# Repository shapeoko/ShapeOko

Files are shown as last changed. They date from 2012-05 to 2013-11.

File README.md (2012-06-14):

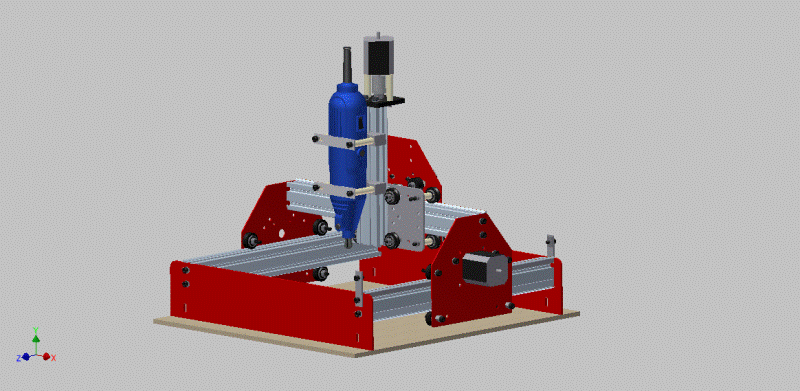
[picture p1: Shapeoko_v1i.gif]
Shapeoko v1i


Goal: ShapeOko's goal is to design and build a fully open source (open hardware) 3 axis CNC machine that anyone can build for about $300. We're doing everything possible to design an easy to assembly, fully capable machine that will do it's part in both the open hardware and desktop manufacturing movements.

#Folder Structure#

##Build_Instructions##
Contains the source files for the PDf build instruction manual (quick start guide). The original document was created in Scribus 1.4.1 an open source Desktop Publishing app that is cross platform compatible. The placed images (PDF files) are all embedded in the document, but can be replaced with the PDF files found in the drawings_pdf folder under the root of the repository. Improvements are encouraged, please contact me for a merge request.

###individual_pages##
Individual pages of the PDF build instruction manual. These are used as targets from the wiki.

##Documents##
Contains informational documentation related to the project. This would include data sheets for purchased electrical components, Bill of Material Information, and an assortment of other miscelaneous documents. Please feel free to suggest more documents that are not currently included.

##drawings_pdf##
PDF exports of the original 2D drawing files. PDF is as universal format as any, publishing in this format will allow anyone to open and view the drawing files without having to install a specialty CAD program. PDF was chosen over DXF for the time being. Community generated DXF files from the original drawings files (drawings_idw) are welcome.

##exploded_png##
There is a non-annotated image at the top of each assiciated page of the wiki. Those images can be found in this directory.

##reference_images##
Image files associated with the project. Logos, and standard views.

##upgrades##
Complete zip files of upgrades for your machine. Currently this is limited to two (2) variations of the standard spindle mount. 

##README.md##
This document in markdown format.

##Shapeoko_v1i##
Image file referenced at the top of this document. 

##Shapeoko_v1i.zip##
Complete Autodesk Inventor Project file for the Shapeoko CNC machine. All part (.ipt), presentation (.ipn), drawing (.idw), and assembly (.iam) files are included in this file. This is probably the place to start if you're looking to import the 3D model. 

###For more information:###
- website: www.shapeoko.com
- wiki: www.shapeoko.com/wiki
- forum: www.shapeoko.com/forum
- twitter: @shapeoko

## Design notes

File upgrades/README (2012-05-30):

Set of drawings, 3D models, images, and gcode files. These sets can be used as a reference to "upgrade" your ShapeOko Machine. Each set is packaged into a seperate zip file. For more information on each set see the "Upgrades" section at www.shapeoko.com

Dremel_mount - Set of UHMW mounts for a Standard Dremel (or generic) rotary tool. Something like this ($13USD) works great: http://www.truevalue.com/product/Fathers-Day/Handy-Dad/Rotary-Tools/40-Pc-Rotary-Tool-Kit/pc/2502/c/2525/sc/2557/36169.uts

DW660_Mount - Set of UHMW (or HDPE or Delrin or anything 3/8" or thicker) mounts for a Dewalt DW660 trim router. You can find this trim router on amazon's website for around $60USD. Link: http://www.amazon.com/DEWALT-DW660-Cut-Out-Rotary-Collets/dp/B000051WQX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

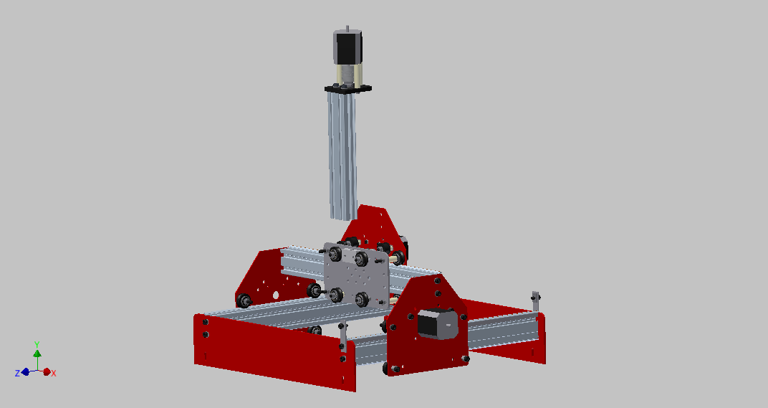
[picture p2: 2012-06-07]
exploded_png/SM-FA03.png

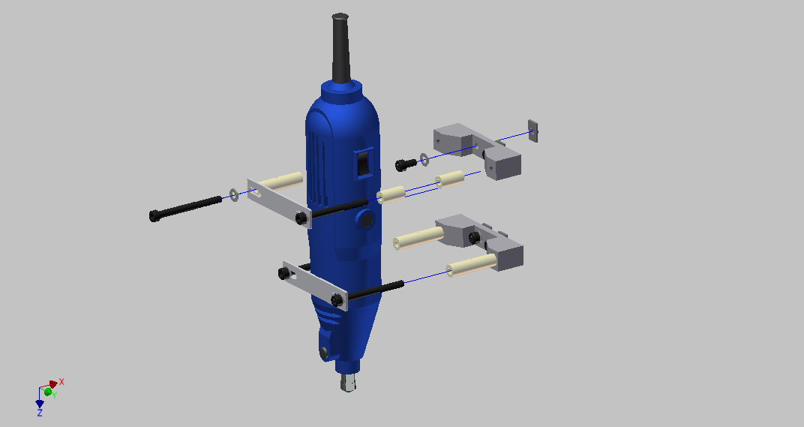
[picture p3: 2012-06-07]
exploded_png/SM-ZA03.png

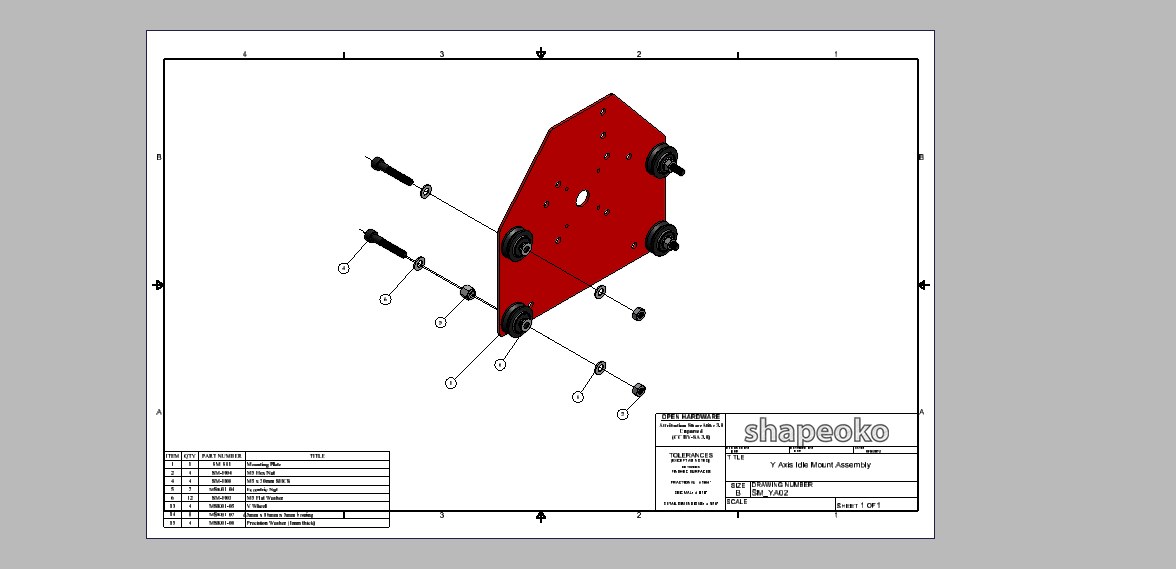
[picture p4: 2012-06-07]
drawings_png/SM-YA02.png

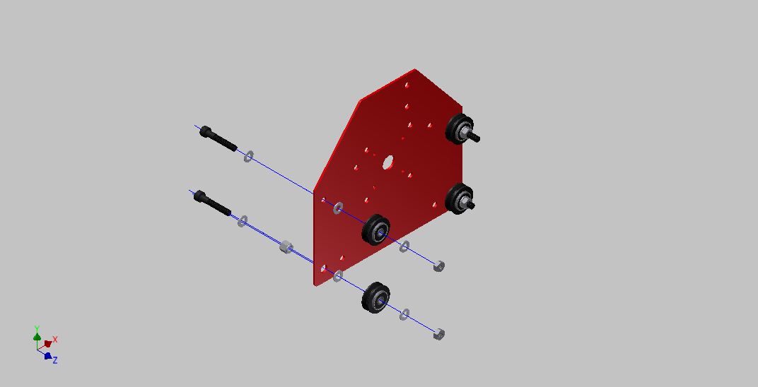
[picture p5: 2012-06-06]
exploded_png/SM-YA02.png

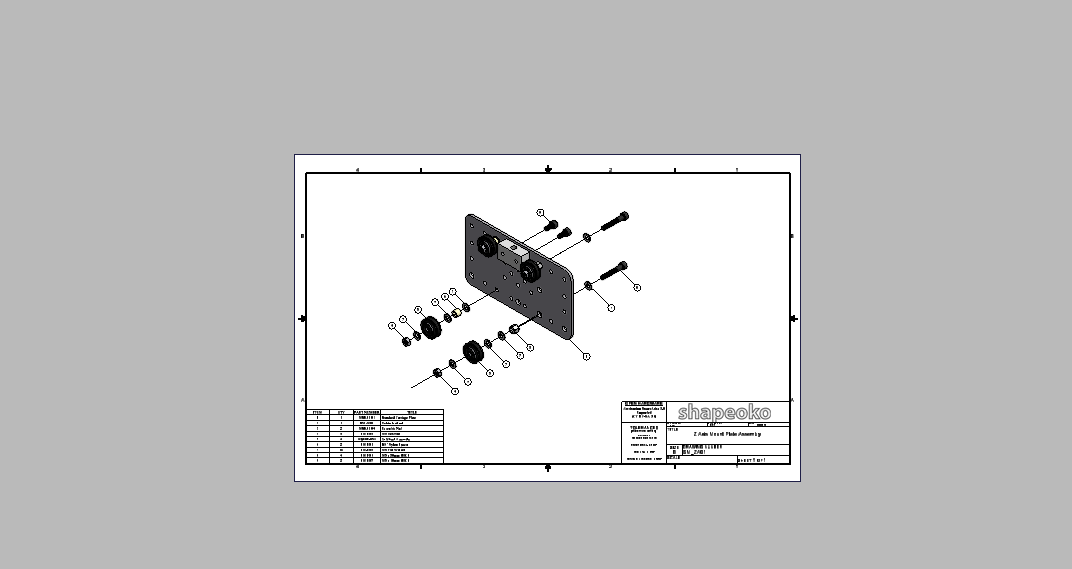
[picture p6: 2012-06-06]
drawings_png/SM-ZA01.png

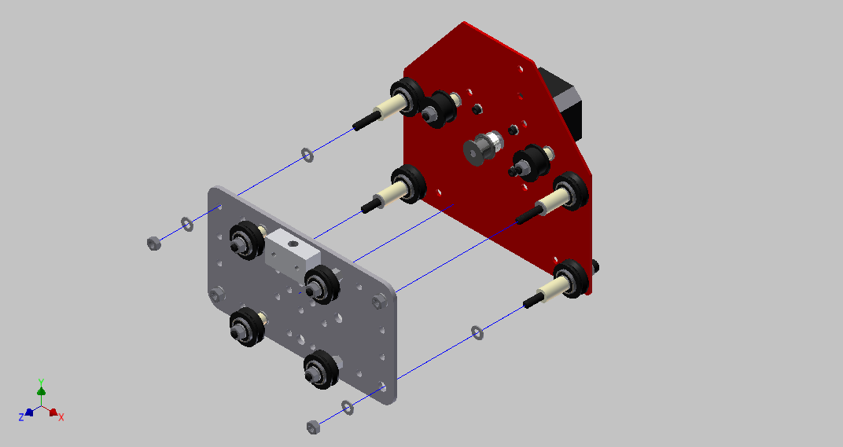
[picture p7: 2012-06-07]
exploded_png/SM-XZA1.png

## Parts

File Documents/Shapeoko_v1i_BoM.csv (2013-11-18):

Item | Project | Estimated Cost | Part Number | BOM Structure | Unit QTY | QTY | Vendor | Stock Number | Title | Web Link
1 | Shapeoko | $3.38 | MKS01-02 | Normal | 1 | 3 | buildlog.net | B17002-375 | Makerslide Extrusion - 375mm | http://store.makerslide.com/index.php?main_page=product_info&cPath=6&products_id=7
2 | Shapeoko | $5.00 | SM-S01 | Normal | 1 | 3 | Shapeoko | SM-S01 | Mounting Plate | www.shapeoko.com/purchase
3 | Shapeoko | $0.02 | SM-H04 | Purchased | 1 | 20 | McMasterCarr | 90592A012 | M5 Hex Nut
5 | Shapeoko | $0.09 | SM-H08 | Purchased | 1 | 16 | McMasterCarr | 91290A254 | M5 x 30mm SHCS
6 | Shapeoko | $2.00 | MSK01-04 | Normal | 1 | 8 | buildlog.net | B18001-001 | Eccentric Nut
7 | Shapeoko | $0.02 | SM-H03 | Purchased | 1 | 100 | McMasterCarr | SM-H03 | M5 Flat Washer
8 | Shapeoko | $5.90 | MSK01-09 | Purchased | 1 | 2 | SDP-SI | A 6T16M018DF6005 | 18 Tooth Timing Pulley | https://sdp-si.com/eStore/PartDetail.asp?Opener=Group&PartID=24069&GroupID=347
9 | Shapeoko | $15.00 | SM-E01 | Purchased | 1 | 3 | buildlog.net | B10-10001 | Nema17 Stepper Motor
10 | Shapeoko | $0.07 | SM-H01 | Purchased | 1 | 6 | McMasterCarr | RSN-10_04-M | 1/4 Nylon Spacer
12 | Shapeoko | $0.04 | SM-H14 | Purchased | 1 | 8 | McMasterCarr | 91290A113 | M3 x 8mm SHCS
13 | Shapeoko | $0.02 | SM-H15 | Purchased | 1 | 8 | McMasterCarr | 91166A210 | M3 Flat Washer
14 | Shapeoko | $0.06 | SM-H07 | Purchased | 1 | 20 | McMasterCarr | SM-H07 | M5 x 10mm SHCS
15 | Shapeoko | $8.00 | MSK01-01 | Normal | 1 | 1 | buildlog.net | C14005 | Standard Carriage Plate
16 | Shapeoko | $2.50 | SM-M08 | Normal | 1 | 1 | Shapeoko | SM-M08 | Delrin lead nut.
17 | Shapeoko | $0.22 | SM-H09 | Purchased | 1 | 8 | McMasterCarr | 91290A264 | M5 x 55mm SHCS
18 | Shapeoko | $0.09 | SM-H02 | Purchased | 1 | 18 | McMasterCarr | 94639A457 | 3/4 Nylon Spacer
19 | Shapeoko | $5.00 | SM-S02 | Normal | 1 | 2 | Shapeoko | SM-S02 | Front/Back Plate
20 | Shapeoko | $0.27 | SM-M05 | Purchased | 1 | 2 | McMasterCarr | 1394A31 | Belt Anchor
21 | Shapeoko | $0.16 | SM-H11 | Purchased | 1 | 6 | Misumi | HNKK5 | Insertion Nut
22 | Shapeoko | $5.00 | SM-S06 | Normal | 1 | 1 | ShapeOko | SM-S06 | Z-Axis Mount Plate
23 | Shapeoko | $0.16 | SM-H13 | Purchased | 1 | 2 | McMasterCarr | 91290A232 | M5 x 16mm SHCS
24 | Shapeoko | $1.00 | SM-M07 | Purchased | 1 | 1 | McMasterCarr | skate_bearing | Z-Axis Bearing
25 | Shapeoko | $0.05 | SM-H10 | Purchased | 1 | 2 | McMasterCarr | 90695A040 | M8 Jam Nut
26 | Shapeoko | $5.58 | SM-H12 | Purchased | 1 | 1 | Ebay | ebay | Coupler
27 | Shapeoko | $1.00 | SM-H05 | Purchased | 1 | 1 | McMasterCarr | 99055A125 | Threaded Rod
28 | Shapeoko | $2.00 | MSK01-03 | Normal | 1 | 1 | buildlog.net | B17022-200 | Makerslide Extrusion - 200mm
29 | Shapeoko | $0.20 | SM-H06 | Purchased | 1 | 3 | McMasterCarr | 91290A137 | M3 x 50mm SHCS
30 | Shapeoko | $5.00 | SM-TM1 | Normal | 1 | 2 | Shapeoko | SM-TM1 | Spindle Mount
31 | Shapeoko | $15.00 | SM-TM3 | Purchased | 1 | 1 | various | Multi-tool | Rotary Tool
32 | Shapeoko | $2.00 | SM-TM2 | Normal | 1 | 2 | Shapeoko | SM-TM2 | Spindle Strap
33 | Shapeoko |  | MDF_Base | Normal | 1 | 1 | various | SM-SWB | 400mm x 450mm MDF
34 |  |  | MSK01-05 | Purchased | 1 | 16 | buildlog.net |  | V Wheel
35 |  |  | MSK01-07 | Purchased | 1 | 40 | buildlog.net | BEARING_5_16_5 | 5mm x 16mm x 5mm bearing
36 |  |  | MSK01-08 | Normal | 1 | 20 | buildlog.net | B18026 | Precision Washer (1mm thick)
37 |  | $2.00 | MSK01-06 | Normal | 1 | 4 | buildlog.net | B17023 | Smooth Idler Drum

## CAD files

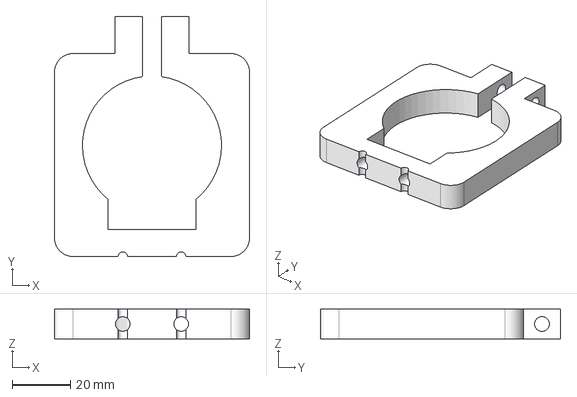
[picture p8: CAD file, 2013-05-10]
upgrades/dremel_mount/uhmw_dremel_mount_1-78.stp
66.8 x 82.2 x 10.2 mm

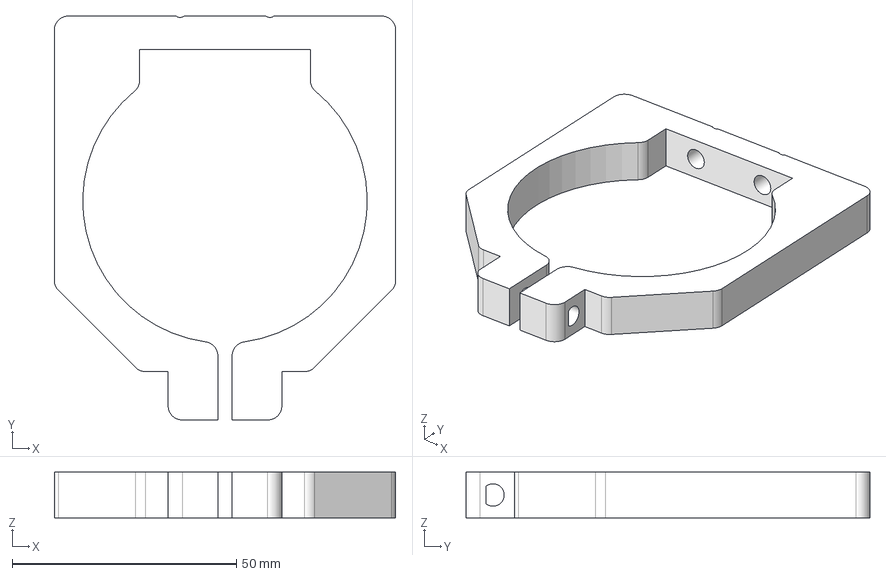
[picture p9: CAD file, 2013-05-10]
upgrades/dw660_mount/DW660_Mount.stp
76.2 x 90.2 x 10.2 mm

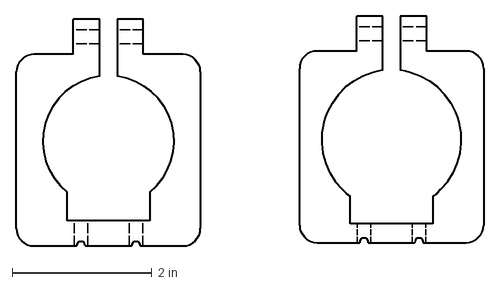
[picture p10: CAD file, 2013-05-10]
upgrades/dremel_mount/uhmw_dremel_mounts.dxf
6.68 x 3.29 in

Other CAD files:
upgrades/dremel_mount/uhmw_dremel_mount_2in.stp
upgrades/dremel_mount/uhmw_dremel_mount_1-78.stl
upgrades/dremel_mount/uhmw_dremel_mount_2in.stl
upgrades/dw660_mount/DW660_Mount.dxf

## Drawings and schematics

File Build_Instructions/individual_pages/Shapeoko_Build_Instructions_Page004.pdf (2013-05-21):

S

h

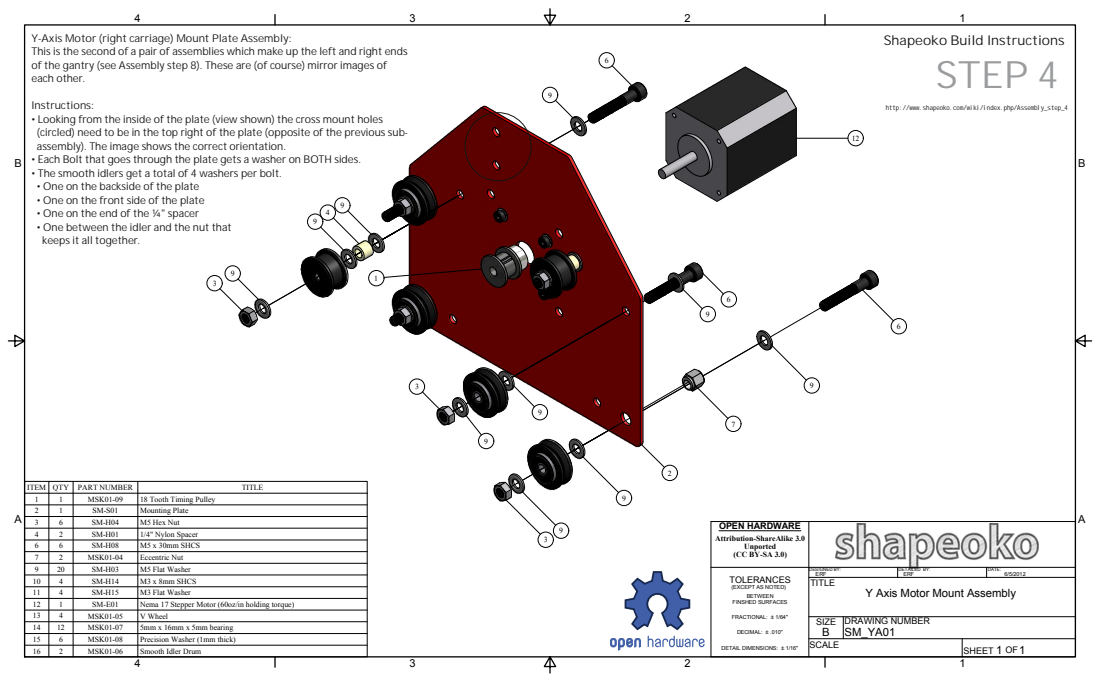
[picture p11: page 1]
uild In; ctio; /www.s; p/Ass; mbly_s; xis; rig; ria; Pla; sse; bly; ste; rse); mir; r. Instruction; s: • Looking fro m; sid; pla; (view; own; cro; ole; (circle; site; revio; bly). T; ows; rie; tio

bly: This is the second of a pair of assemblies which make u

peoko.com/wiki/index.ph

n. • Each Bolt that goes through the plate gets a washer
s. • The smooth idlers get a total of 4 washers per bolt. • One on the backside of the plate • One on the front side of the plate • One on the end of the ¼" spacer • One between the idler and the nut that keeps it all together.

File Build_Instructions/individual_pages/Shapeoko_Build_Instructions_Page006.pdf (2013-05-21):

S

h

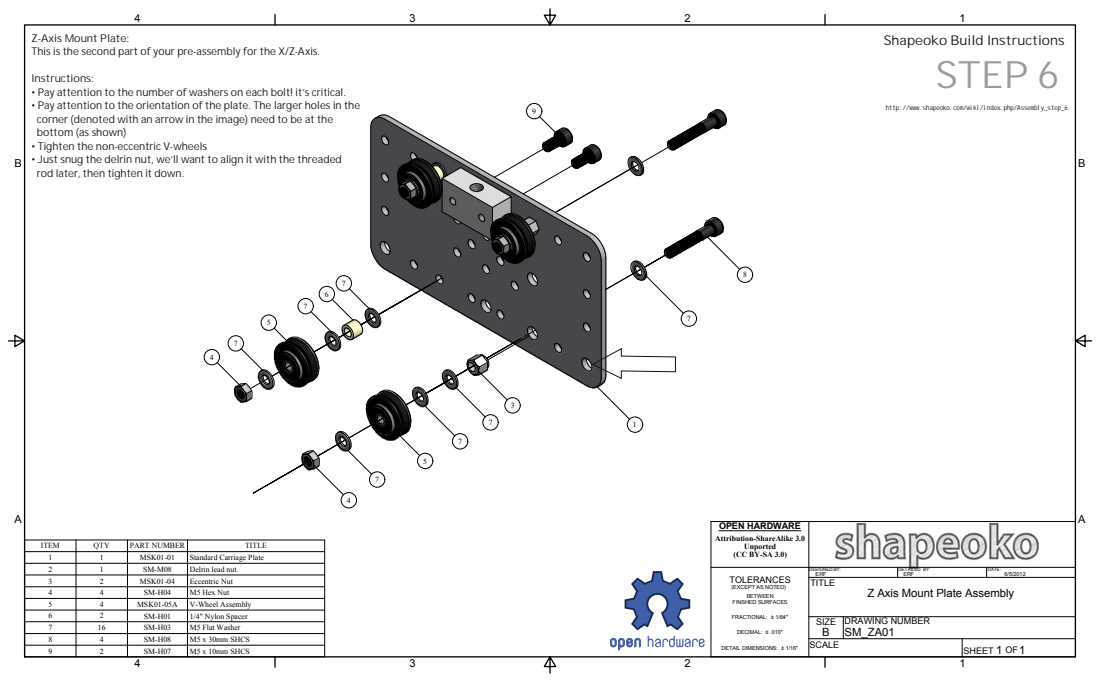
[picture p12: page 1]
uild In; tio; www.s; wiki/in; mbly; xis; Pla; bly; wit; Tig; ric; els; elrin; alig; tig

e: This is the second pa

xis. Instructions: • Pay attention to the number of washers on each bolt! it’s critic

al. • Pay attention to the orientation of the plate. The larger holes in t

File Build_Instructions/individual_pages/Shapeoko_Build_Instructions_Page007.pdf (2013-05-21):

S

h

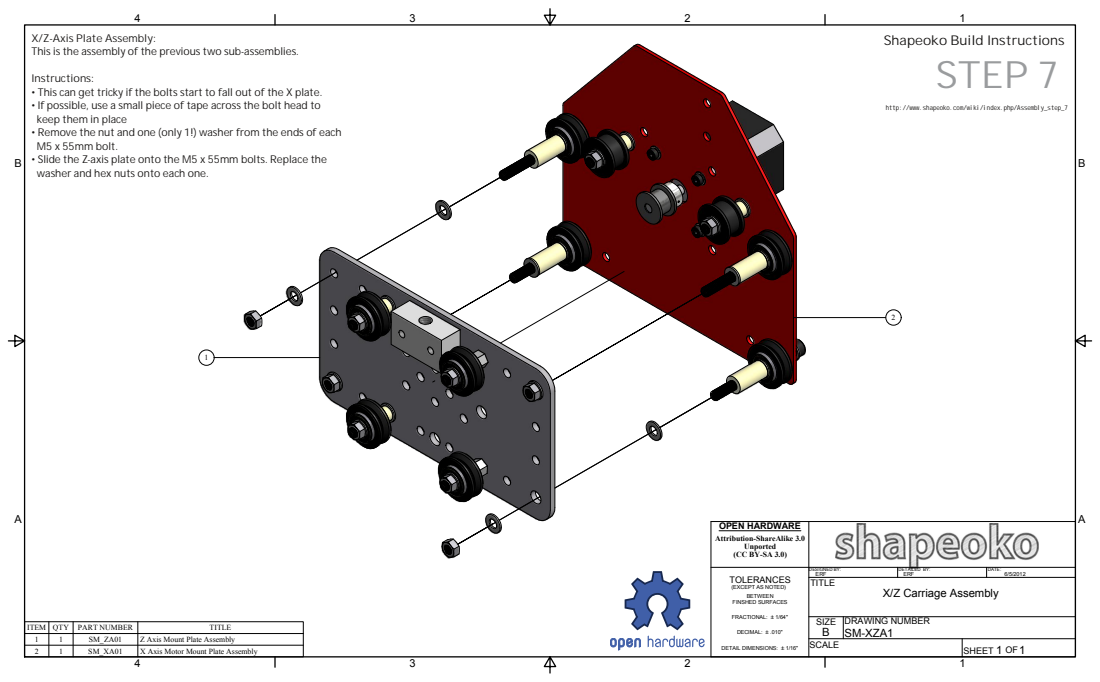
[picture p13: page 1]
uild In; tio; www.s; wiki/in; mbly_s; xis; Pla; vio; sse; blie; olt; pla

bly: This is the assembly of the

s. Instructions: • This can get tricky if the bolts start to fall out of the X pla

e. • If possible, use a small piece of tape across the bolt head to keep them in place • Remove the nut and one (only 1!) washer from the ends of e

olt. • Slide the Z-axis pla

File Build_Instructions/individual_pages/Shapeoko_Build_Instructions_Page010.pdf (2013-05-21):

S

h

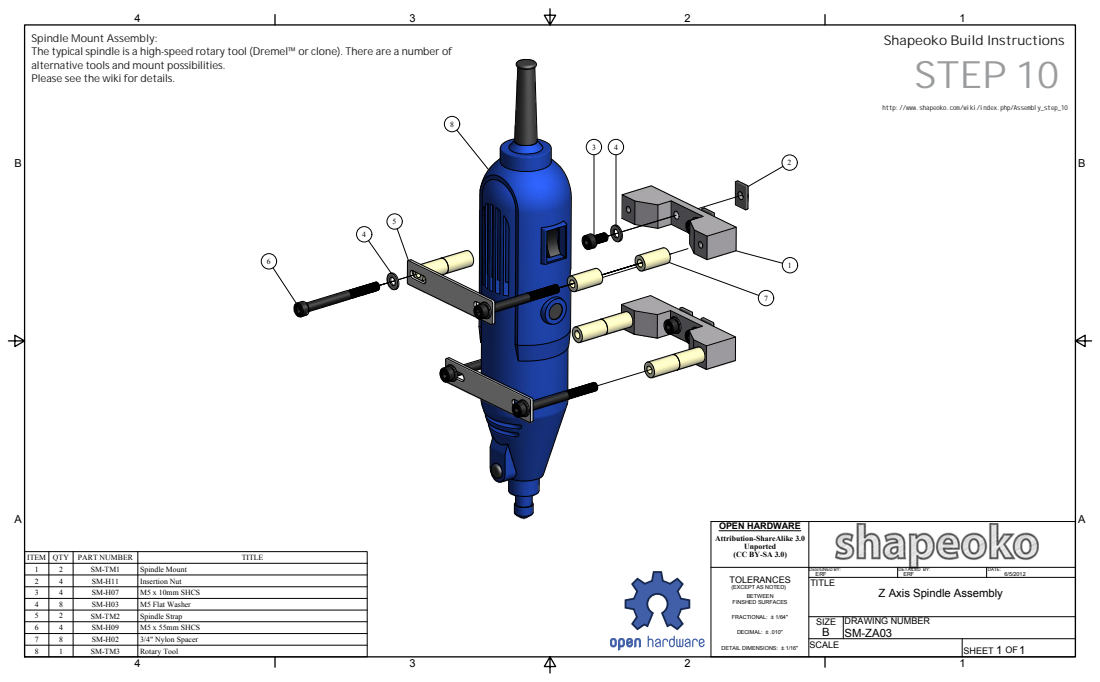
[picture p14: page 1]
uild In; tio; www.s; wiki/in; mbly_s; pin; dle; clo; alt; tiv; ols; ssibilitie

bly: The typical spindle is a high

s. Please see the wiki for details.

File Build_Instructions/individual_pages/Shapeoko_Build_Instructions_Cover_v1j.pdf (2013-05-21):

# Build Instructions

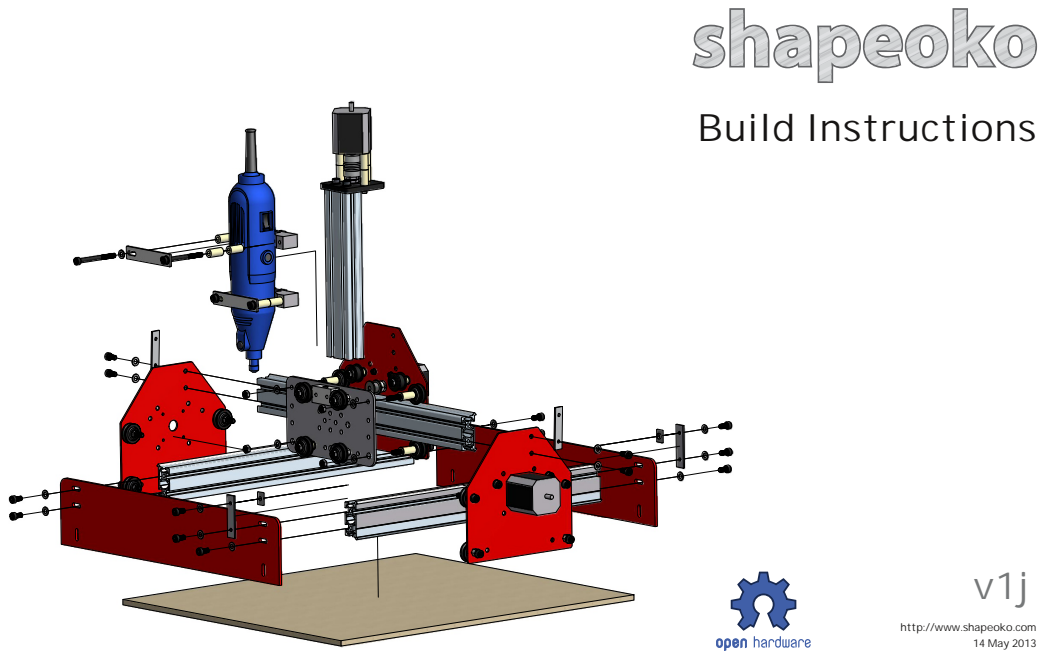
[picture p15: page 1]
14 May 2013

http://www.shapeoko.com

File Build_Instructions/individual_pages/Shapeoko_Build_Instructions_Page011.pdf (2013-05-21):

S

h

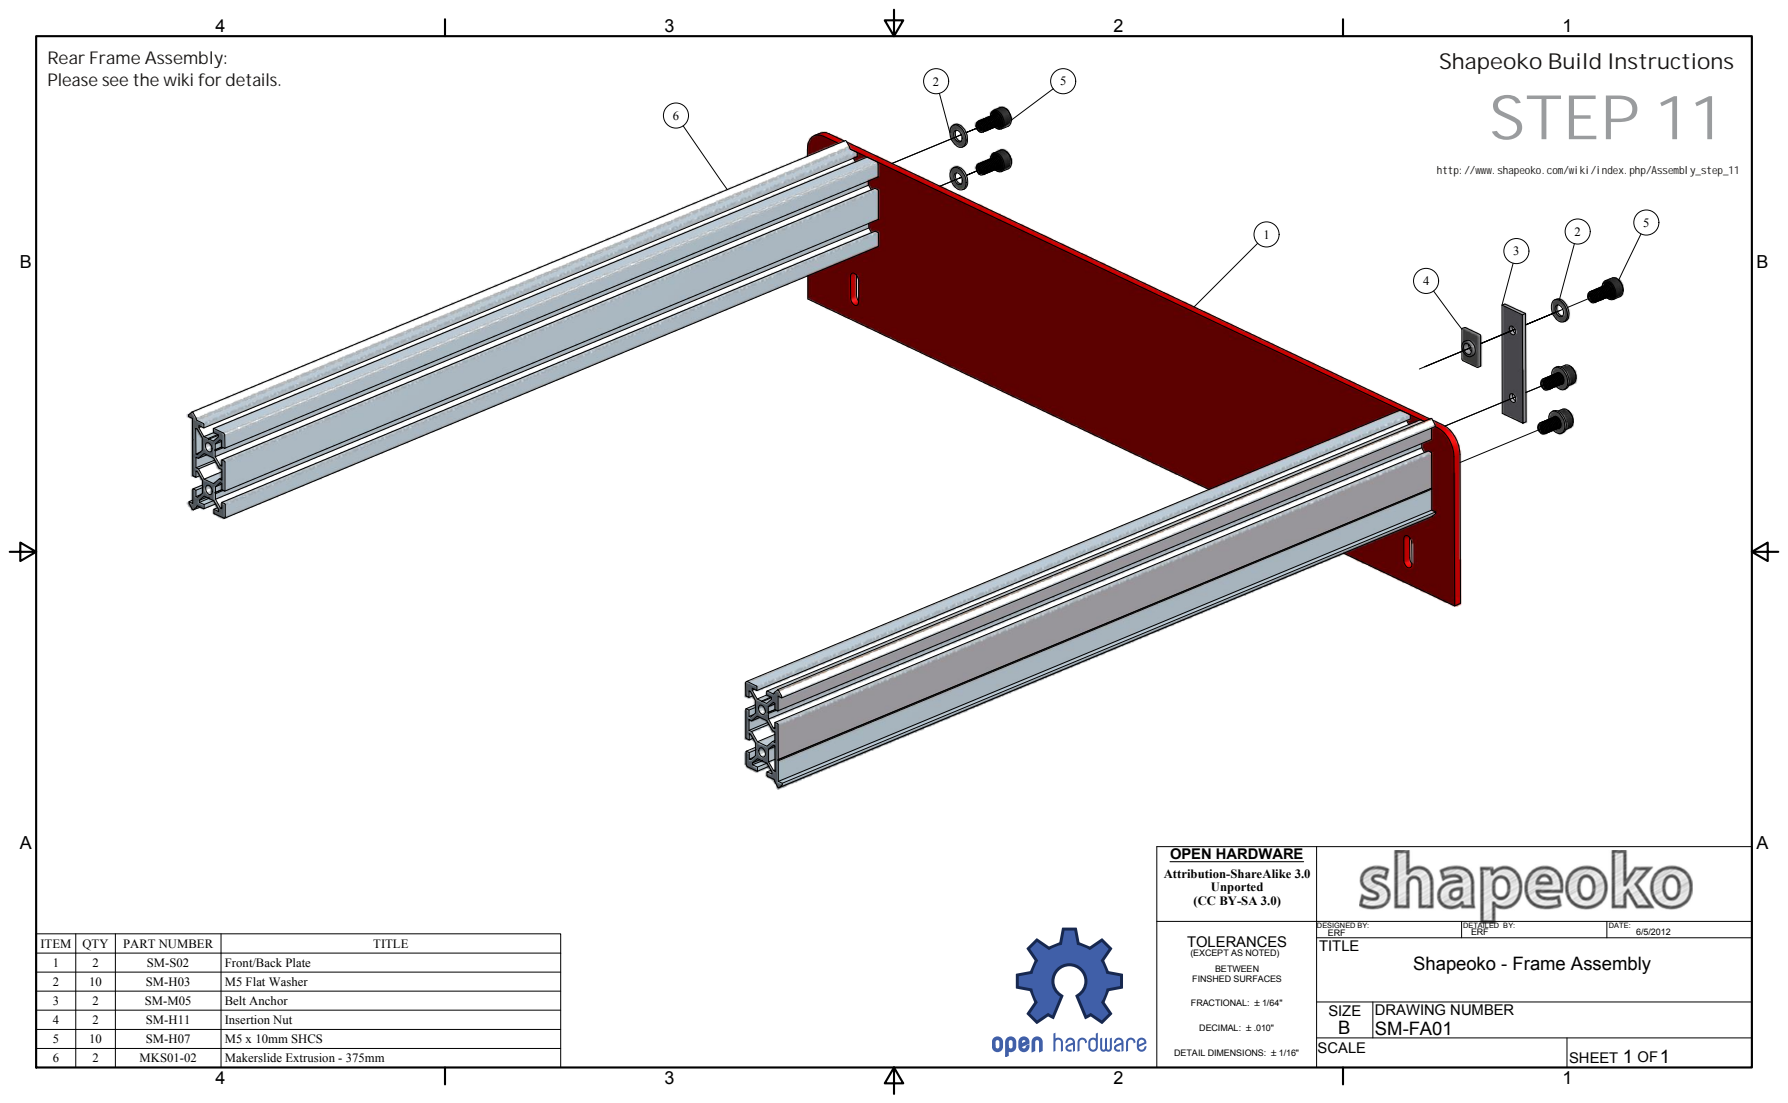
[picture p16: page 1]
uild In; tio; www.s; peoko.com/; wiki/index.p; mbly_s; sse; ails.

bly: Please see the wiki for

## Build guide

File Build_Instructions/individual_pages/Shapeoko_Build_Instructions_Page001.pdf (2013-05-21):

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
### uild In

s

t

r

u

c

### tio

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
www.s

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
wiki/in

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
mbly_s

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
el A

s

s

e

m

bly: The V-Wheels and M
a

k

e

r

slid

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
e in

alig

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
allo

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
xis. W

h

e

n

a

sse

m

blin

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
cisio

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
s. T

h

e
p

r

e

cisio

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
t. Instructions: • Insert a bearing into one side. These are force fit tolerances so you might have to push hard. • Press the bearing until it’s seated against the inside lip of the V-Wheel. • Slide an M5 bolt through the bearing (outside in) — you’ll use this to align the precision washer and the other bearing. • Slide the precision washer over the bolt and let it slide all the way down until it is touching the bearing you just inserte

•

Slid

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
d le

t it

slid

e

d

o

wn

u

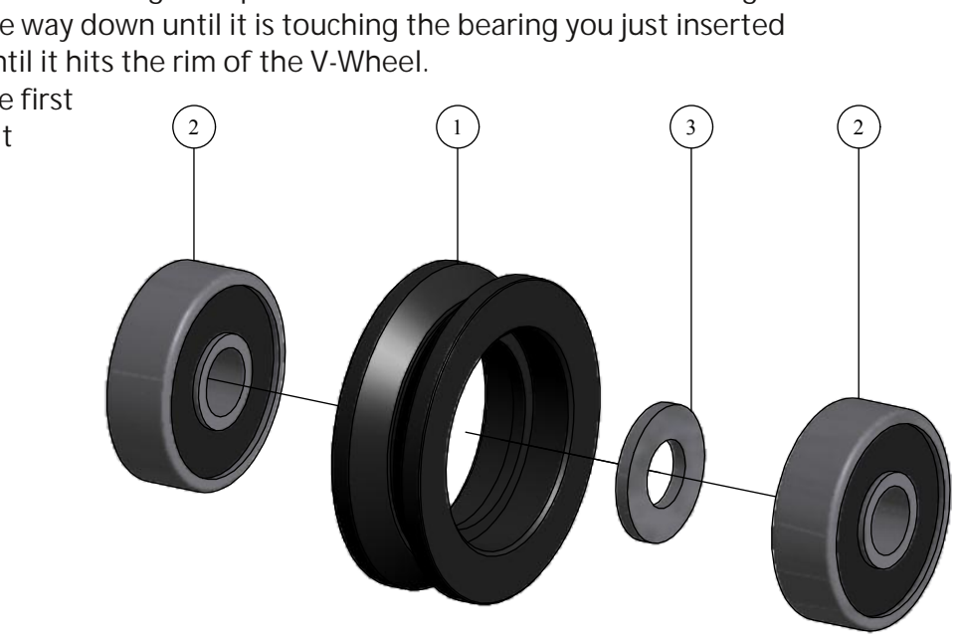
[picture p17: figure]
til it; hit; rim

n

el. • Press the second bearing into the V-wheel just as you did the first • When the assembly is complete, you can remove the M5 bolt Note: do not forget the precision washer!

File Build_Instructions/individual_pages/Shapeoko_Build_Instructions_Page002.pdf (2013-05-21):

### Shapeoko Build Instructions

# STEP 2

http://www.shapeoko.com/wiki/index.php/Assembly_step_2

Smooth Idler Assembly:
The Idler Wheels align the belts so that they can grip the pulleys. When assembling the wheels a precision washer (1mm thick) goes between the bearings. The precision washers are specced to be 1mm thick and provide a surface for the races to contact, keeping everything tight.

Instructions:
- Insert a bearing into the open side side. These are force fit tolerances so you might have to push hard.
- Press the bearing until it’s seated against the inside lip of the idler drum.
- Slide an M5 bolt through the bearing (outside in) — you’ll use this to align the precision washer and the other bearing.
- Slide the precision washer over the bolt and let it slide all the way down until it is touching the bearing you just inserted
- Slide the other bearing over the bolt and let it slide down until it hits the rim of the drum.
- Press the second bearing into the drum just as you did the first until it is tight against the precision washer
- When the assembly is complete, you can remove the M5 bolt

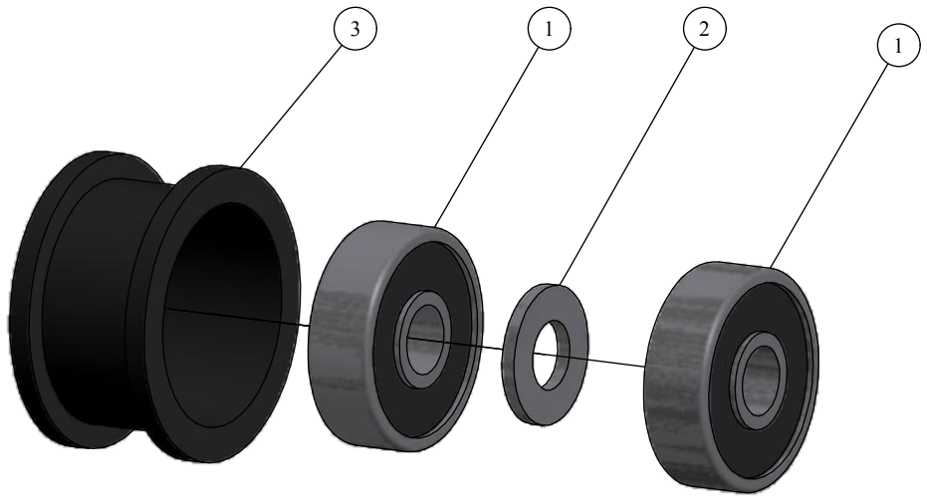
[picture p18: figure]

Note: do not forget the precision washer!

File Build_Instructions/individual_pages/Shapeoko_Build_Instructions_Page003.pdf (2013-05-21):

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
### uild In

s

t

r

u

c

### tio

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
www.s

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
wiki/in

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
mbly

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
xis Idle

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
bly: A pair of assemblies make up the left and right end s

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
). T

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
r im

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
r. Instructions: • Take note of the top hole orientation. • Looking from the inside of the plate (view shown) the cross mount

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
e in

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
e. • If you assemble these backwards you’ll have to dis a

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
flip

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
d. • It’s not the end of the world, b u

t it

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
g if

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
e. • Make sure the smaller end of the ecc e

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
s in

t

o

t

h

e

h

ole in the plate. If you install the spacer backwards you won't be able to adjust the spacing of the V-Wheels. • If the steel plate has been painted, the tapered end of the eccentric spacer may be very difficult to fit into the hole. Remove the paint from the inside of the hole with an appropriate tool (a drill bit, or the threads of a screw will work) • The thick sidewall of the eccentric spacer should face the other V-wheel, in this way t

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
els is la

r

g

e

s

t, w

hic

h

will help the later assembly onto the Makerslide rail. • To avoid later confusion, the thicker side of the ecc

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
d, e.g. wit

h

a

p

e

n.

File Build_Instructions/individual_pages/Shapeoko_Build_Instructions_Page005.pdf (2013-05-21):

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
### uild In

s

t

r

u

c

### tio

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
www.s

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
wiki/in

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
mbly_s

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
e: Similar to the previous two s

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
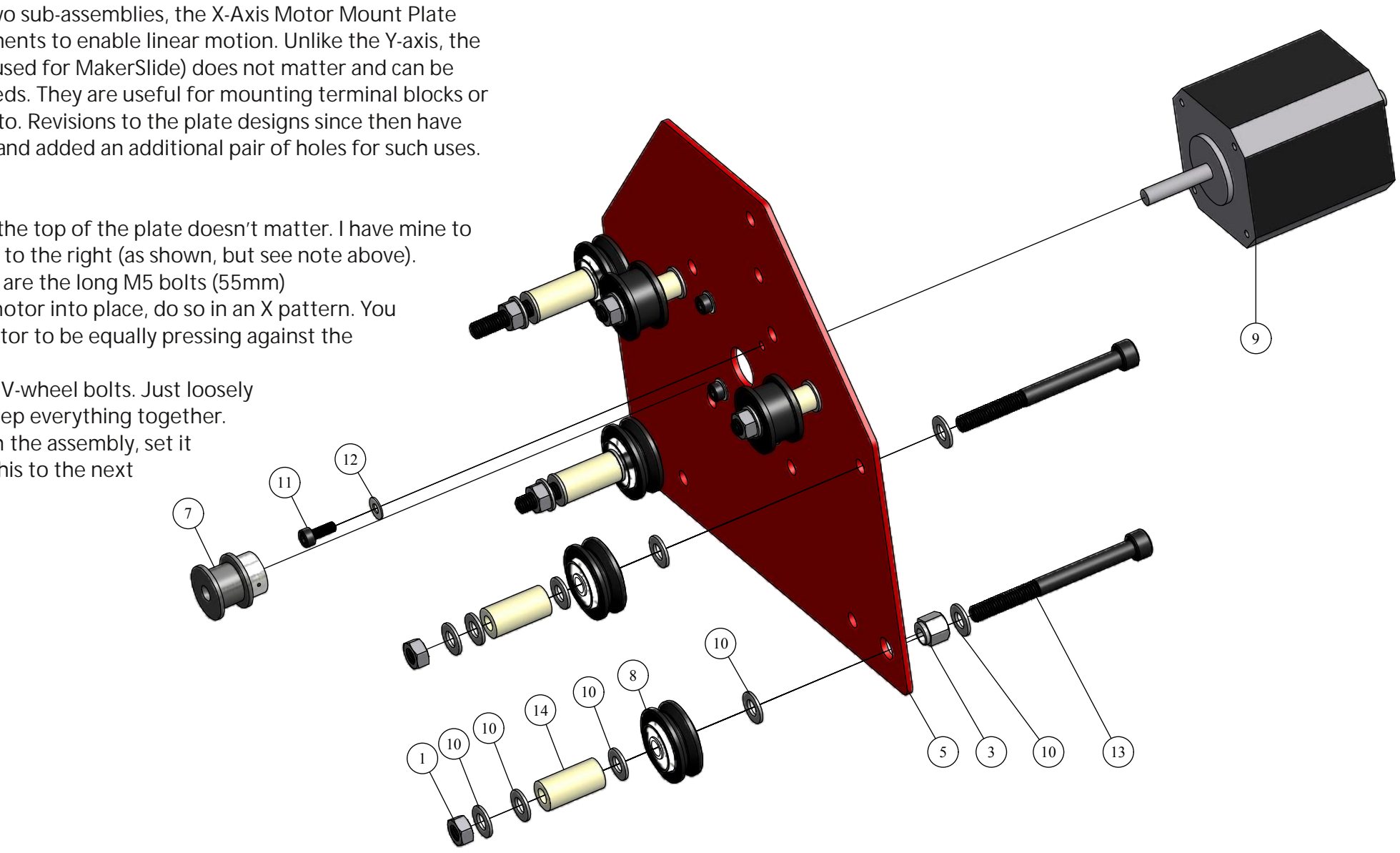
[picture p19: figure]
sse; blie; xis; Pla; ble lin; tio; nlik; Slid; tin; min; al blo; visio; pla; sig; sin; ditio; air; ole

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
all co

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
rical a

s. Instructions: • The hole orientation at the top of the plate doesn’t matter. I have mine to the left, but they can be to the right (as shown, but see note above). • The bottom set of bolts are the long M5 bolts (55mm) • When you tighten the motor into place, do so in an X pattern. You want the face of the motor to be equally pressing against the plate. • Don’t tighten down the V-wheel bolts. Just loosely thread on the nuts to keep everything together. • When you are done with the assembly, set it aside, you’ll be bolting this to the next assembly build.

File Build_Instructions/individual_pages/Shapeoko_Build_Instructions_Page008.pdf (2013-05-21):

### Shapeoko Build Instructions

# STEP 8

http://www.shapeoko.com/wiki/index.php/Assembly_step_8

Full Gantry Assembly:
This is the assembly of the previous three sub-assemblies. The image does not show the belt anchors in place. These are best added after the machine is otherwise completely assembled since they have sharp corners and are harder than the Makerslide.

Note: The Makerslide must be tapped before assembly. Please see the wiki, or the instructions which came w/ your tapping tool.

Instructions:
- Clean ends of extrusion of any debris.
- Snug bolts on Gantry - Y Idle Mount Plate.
- Slide X/Z Assembly onto Makerslide Extrusion
- Snug Bolts on Gantry - Y Motor Mount Plate
- Work your way from each side in a X pattern.
- Align top of extrusion with top of plate.
- Keep square

Note: Ensure eccentric wheels on SM-XZA1 are set to their widest position before attempting to slide onto Makerslide.

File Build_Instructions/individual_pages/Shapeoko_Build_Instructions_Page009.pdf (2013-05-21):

S

h

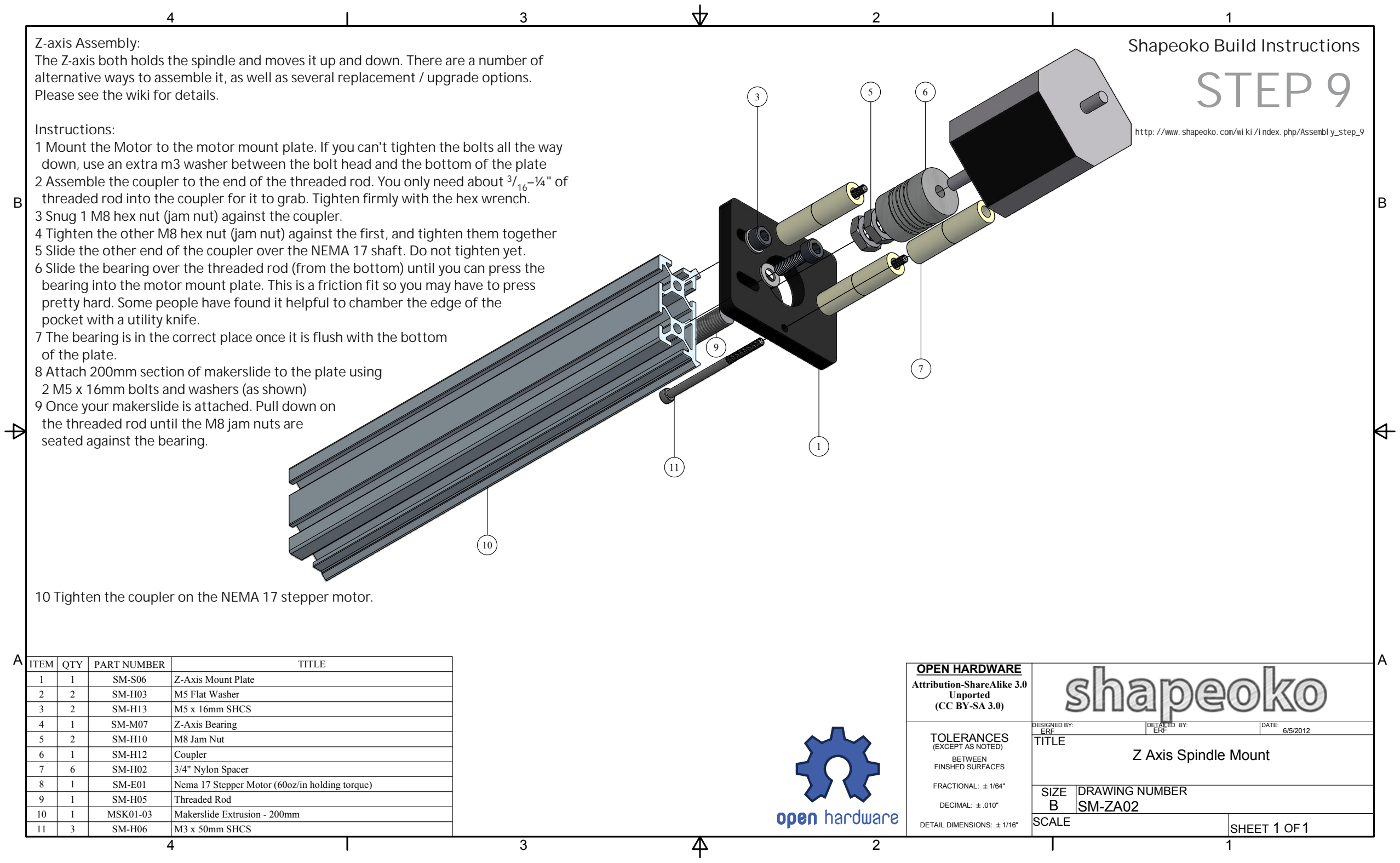
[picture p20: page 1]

a

p

e

o

k

o

B

### uild In

s

t

r

u

c

### tio

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
www.s

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
wiki/in

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
mbly_s

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
bly: The Z-axis both h
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
s it

u

p

a

n

d

d

o

wn. T

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
ble it

,

a

s

well a

s

se

v

e

r

al r

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
s. Please see the wiki for details. Instructions: 1 Mount the Motor to the motor mount plate. If you can't tighten the bolts all the

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
d. Y

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
d in

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
r it

t

o

g

r

a

b. Tig

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
h. 3 Snug 1 M8 hex nut (jam nut) against the coupler. 4 Tighten the other M8 hex nut (jam nut) against the first, and tighten them toge

t

h

e

r
5

Slid

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
ft. D

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
t. 6 Slide the bearing over the threaded rod (from the bottom) until you can press t

h

e
b

e

a

rin

g in

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
e. T

his is

a

f

rictio

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
d. S

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
d it

h

elp

f

ul t

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
tilit

y

k

nife. 7 The bearing is in the corre ct

pla

ce

o

n

ce it is

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
e. 8 Attach 200m
m

se

ctio

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
slid

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
slid

e is

a

t

t

a

c

h

e

d. P

ull d

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
til t

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
g. 10 Tighten the coupler on th

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
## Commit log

2012-02-16 adding schematics directory
2012-05-30 added part files
    Each part is saved as a stp (step) file. Import into your CAD program of
    choice to view in 3D space.
2012-05-30 Cleaned up Directory Structure, added DW660
    Cleaned up the directory, removing obsolete folders/readme files. Added
    the Dewalt DW660 series of UHMW mounts and renamed Dremel UHMW mounts to
    something more sane. Updated readme to include links to mentioned tools.
2012-05-30 Updated readme file (with instrucitons)
    In order to make this manageable, the assemblies will be included as stp
    files. Each one can then be imported as a part file into your favorite
    3D modeling program. If you'd prefer to have component level control
    over your model, you can build the assemblies from the individual part
    files (./part_files/*.stp).
    To make things even more flexible, the complete original 3D model, in
    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
2012-06-01 Updated readme file
    Sudo directions on how to open the assembly with Inventor 2012
2012-06-01 Moved old top level to Assemblies folder
    seemed like a more logical level than in the root.
2012-06-01 Added detailed Bill of Material
    Shared in standard CSV format. Web links were included for some items
    but not all. 'Stock Number' column is the actual Vendor Part number so
    finding the part should be easy.
    [BoM_Shapeoko_v1i.csv]
2012-06-01 Adding space delimited BoM for online viewing
2012-06-07 Restructuring Layout
    mirroring my local directory to make changes easier to commit. github
    does not support all of the inventor files, so true replication is still
    not possible. Zipping inventor specific files together is the only way
    to commit them.
    [BoM_Shapeoko_v1i.csv, Shapeoko_v1i_BoM.csv]
2012-06-14 added supplemental z-axis assembly drawing
    cutout view of assembled z-axis
2013-04-13 unzipped upgrade files and reworked directory structure
    [DW660_Mount.dxf, DW660_Mount.stp, uhmw_dremel_mount_1-78.stl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]
2013-11-18 changing so renderable.
    [Shapeoko_v1i_BoM.csv]
